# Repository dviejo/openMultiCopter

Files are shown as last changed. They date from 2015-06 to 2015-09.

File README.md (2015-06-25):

### Multi Copter Project ###

* Created by Diego Viejo

* Date of creation: 09/May/2015

* Distributed under Apache License V2.0

## Description ##

This project is for developing a working multi copter drone chassis. It is fully designed using [OpenScad](http://www.openscad.org "OpenScad"). The project arises after the great quadcopter design of Daniel Norée that you can find [here](http://www.thingiverse.com/thing:793425 "here"). This is robust and aesthetically perfect quad. But it don't fit different electronics nor copter's gears. As Daniel has its design frozen, I decided to make my own and take his as an inspiration. 

I'm trying to keep copter arms fully compatible with those from Daniel's design. So it will be possible to use his arms in my copter body and vice-versa.

My idea is to make this project fully parameterizable: the number of arms, size for the body, battery compartment and so on. 

For some parts of this project I'm using the nice writing routines from Harlan Martin. The complete package can be downloaded from [his repository on github](https://github.com/rohieb/Write.scad "writescad").

## Current Status: Design and Test

* Copter arm is finished. (Already printed and tested)
* Quadcopter body is finished (Already printed and tested)
* Quadcopter body cover is finished (Already printed and tested)
* Quadcopter battery compartment is finished (Already printed and tested)

** First Flight Performed!!!! ** 

[https://youtu.be/LpXG32mkR34](https://youtu.be/LpXG32mkR34)
[https://youtu.be/p5fSE5LHzbQ](https://youtu.be/p5fSE5LHzbQ)
[https://youtu.be/718BIuiu2yI](https://youtu.be/718BIuiu2yI)
[https://youtu.be/-O9PJhnjDc4](https://youtu.be/-O9PJhnjDc4)

## Pictures

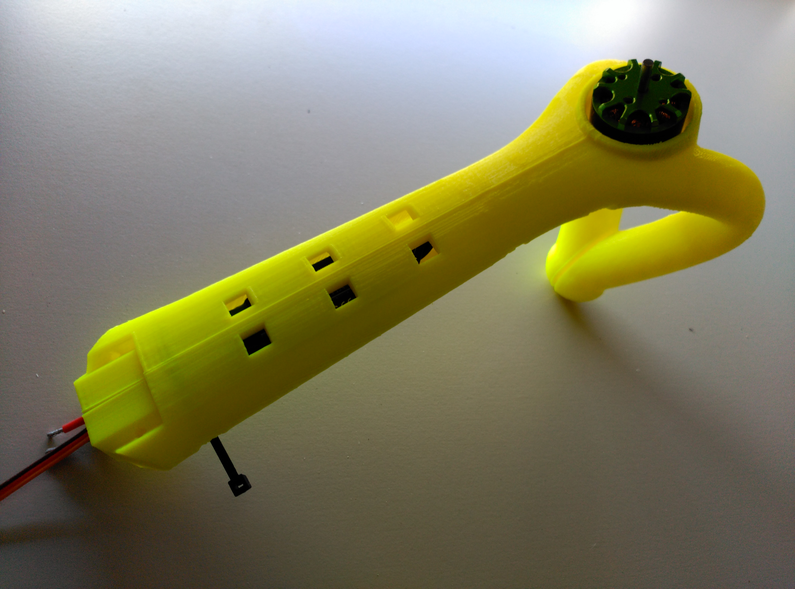
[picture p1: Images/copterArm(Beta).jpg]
copter arm mounted copter arm


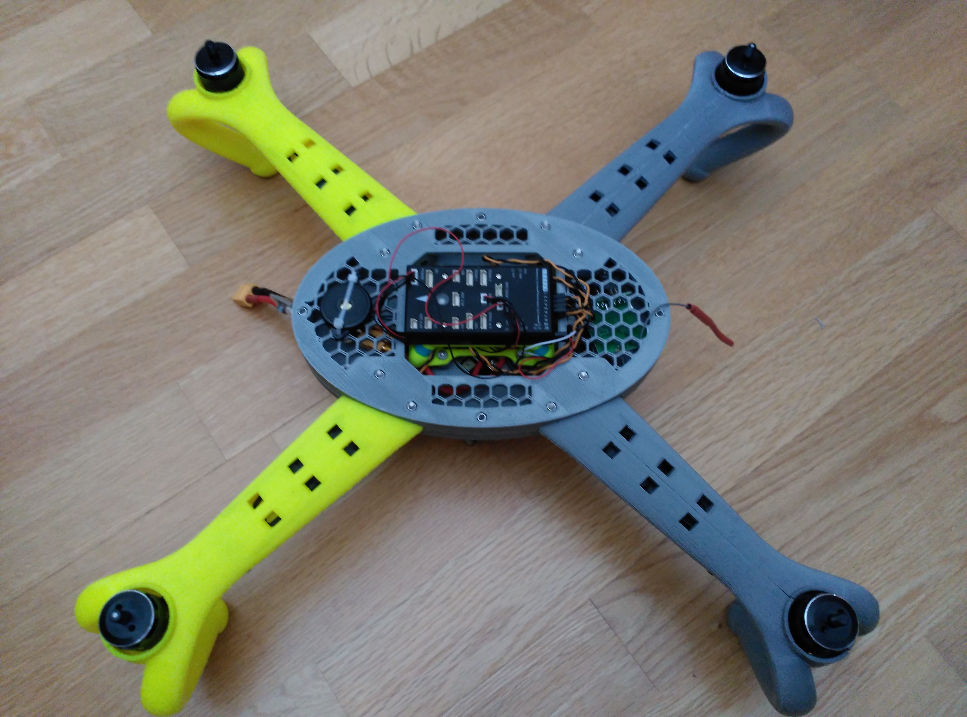
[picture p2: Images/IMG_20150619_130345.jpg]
main frame mounted main frame and arms


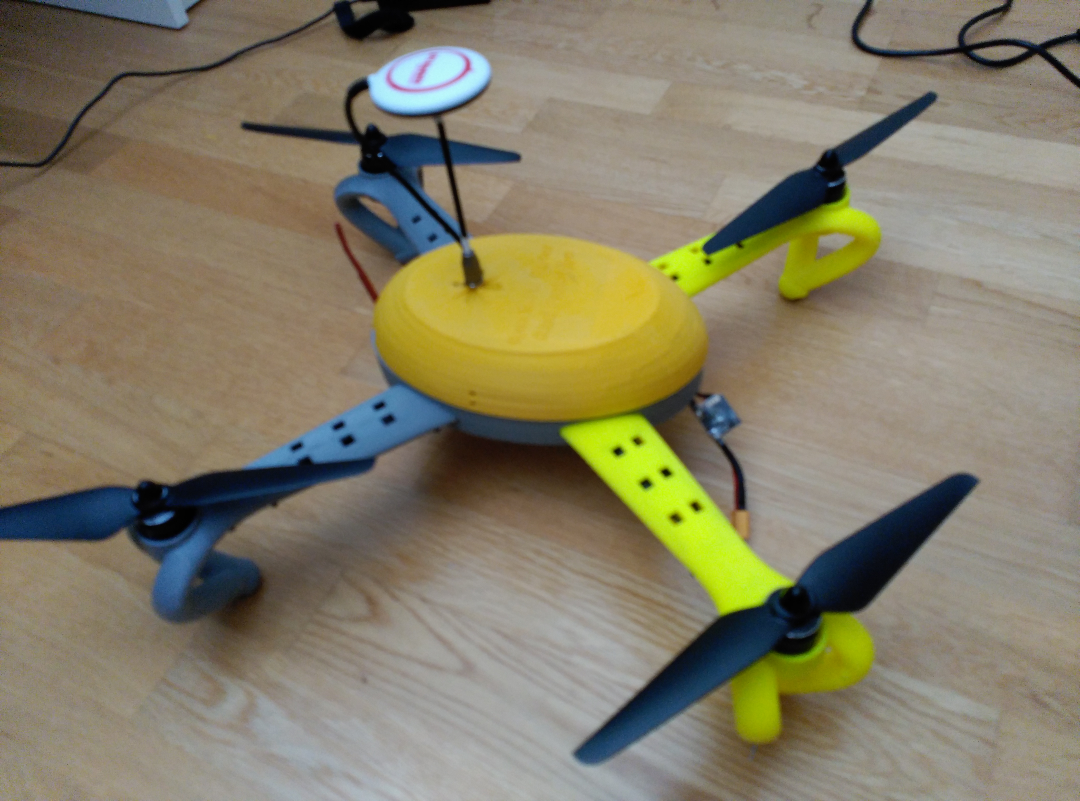
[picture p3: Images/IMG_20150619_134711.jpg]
complete copter V1 main frame and arms


More pictures can be found at [github repository](https://github.com/dviejo/openMultiCopter/tree/master/Images "github repository")

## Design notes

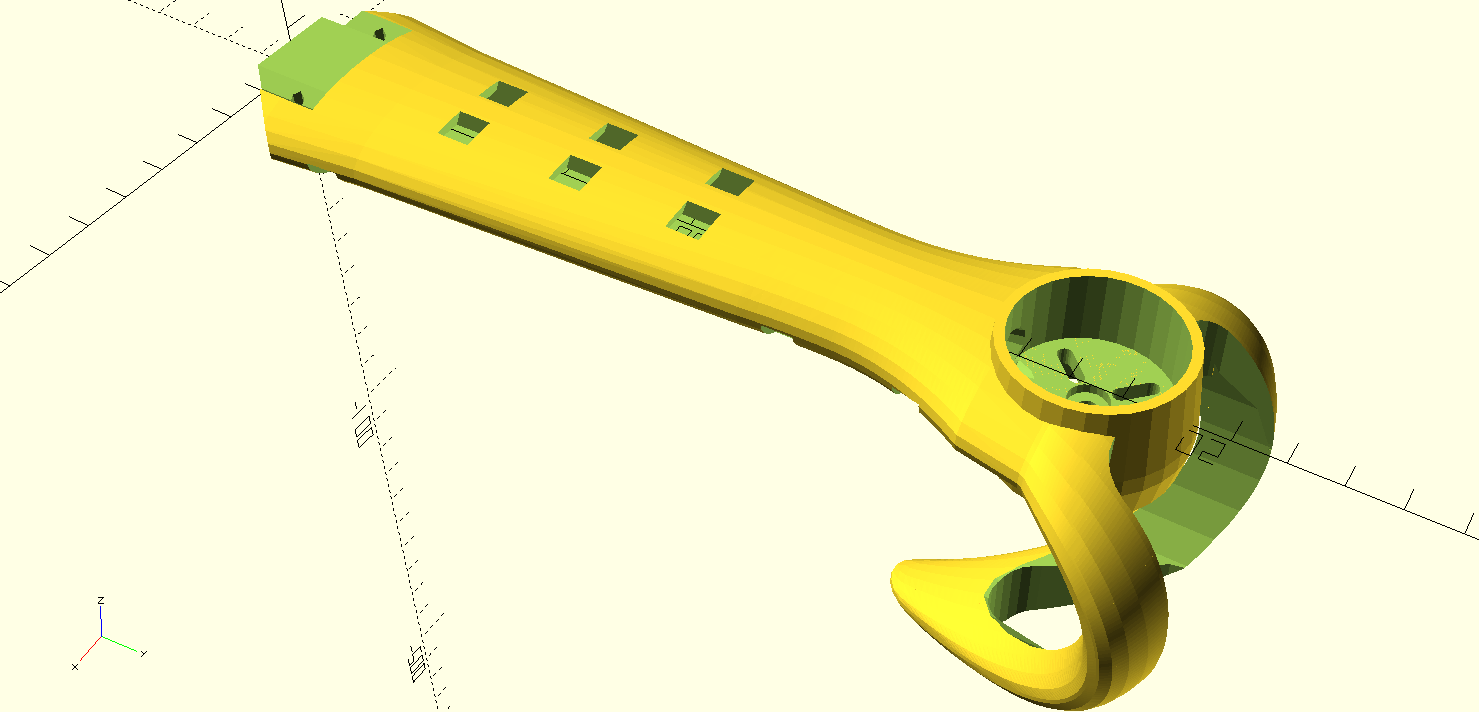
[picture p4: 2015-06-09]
Images/CopterArmComplete.png

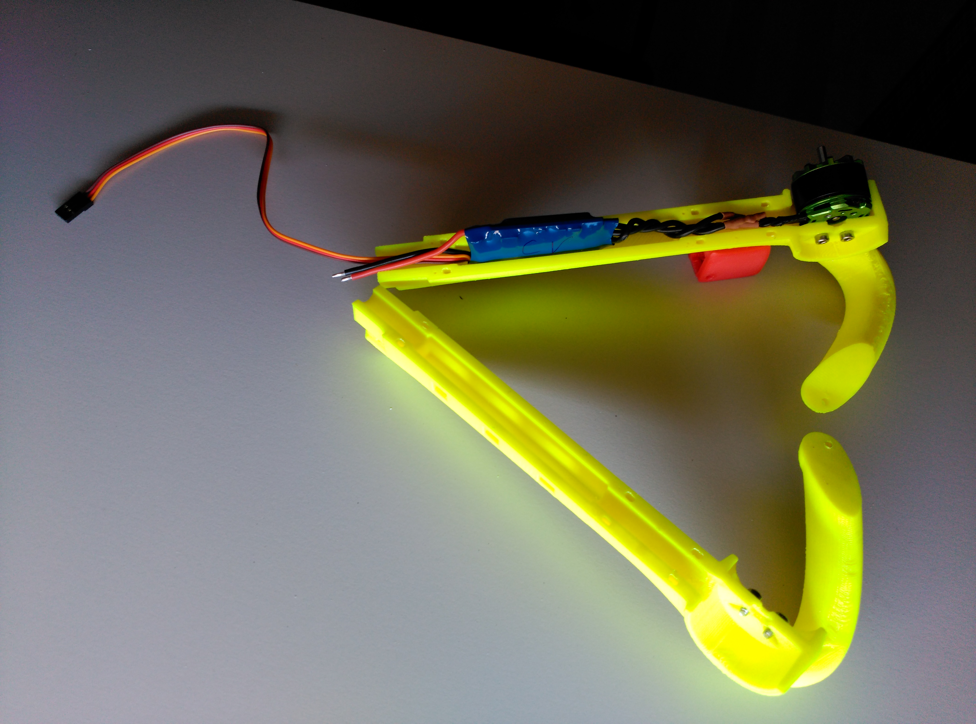
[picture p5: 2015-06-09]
Images/copterArm2(Beta).jpg

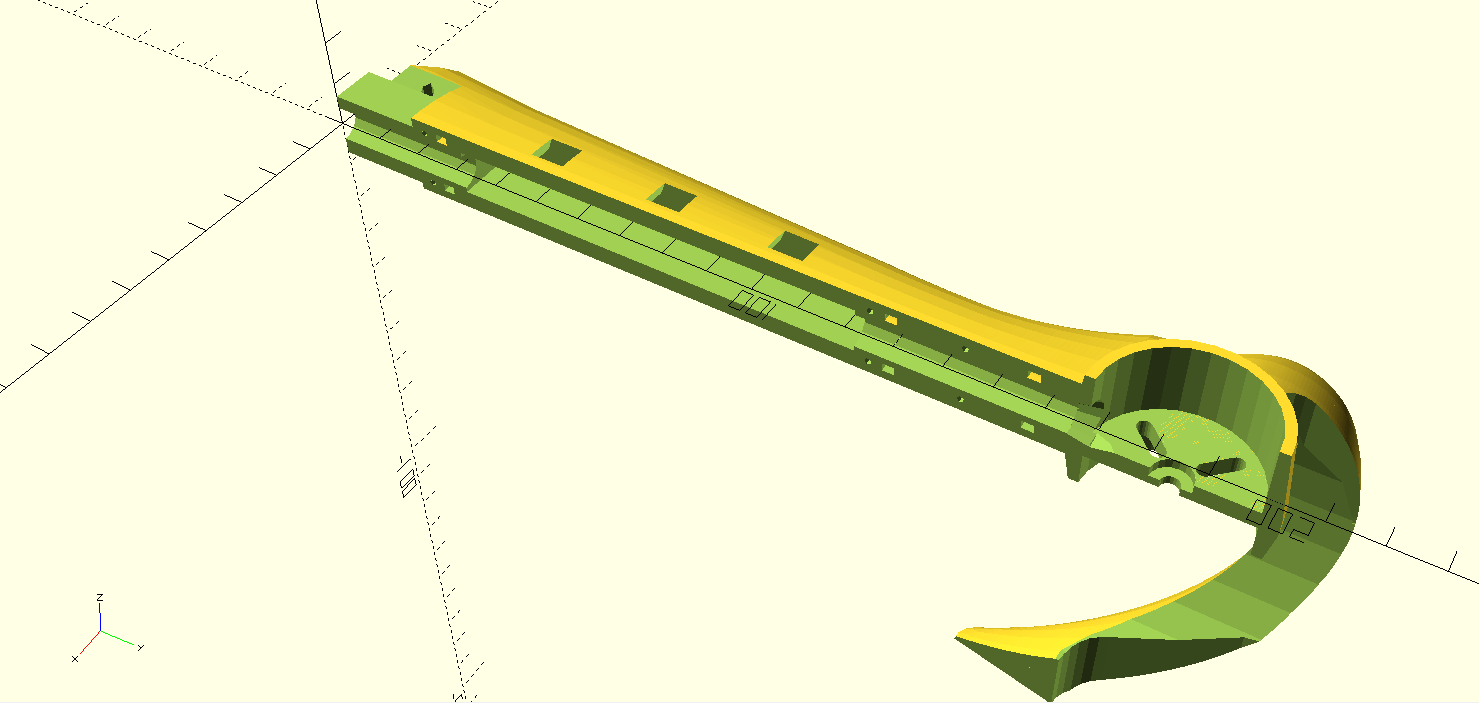
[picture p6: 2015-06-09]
Images/CopterArmPart1.png

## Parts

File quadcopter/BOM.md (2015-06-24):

# Open Multi Copter - Quad BoM #

## Bill Of Materials ##

> All the components that I used for building up this quad copter has been purchased from [RC-Innovations](rci-innovations.com "RC-Innovations") or [Hobbyking](http://www.hobbyking.com "Hobbyking"). Nevertheless, as this project is parametrizable, you can use any component you want and adapt the copter chassis to it.

1. Motors and propellers

 - [T-Motor AIR GEAR 350 Set](https://rc-innovations.es/Motores-multirrotores-aeromodelismo-brushless/TMotor-motores-para-multicopteros-drones-RC-Innovations-distribuidor-oficial/T-motor-pack-mot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 "T-Motor AIR GEAR 350 Set") 120€. This set includes 4 920kv motors, 4 20A ESCs and 4 (2CW + 2CCW) propellers
 
 - Alternatively, you can purchase [Multistar 350QX Blade Motor set](http://www.hobbyking.com/hobbyking/store/__54277__Multistar_350QX_Blade_Motor_set_4pcs_Box_2209_1200KV.html "Multistar 350QX Blade Motor set") (~59€) or [Multistar Elite - 2216-920 Box set](http://www.hobbyking.com/hobbyking/store/uh_viewItem.asp?idProduct=74770 "Multistar Elite - 2216-920 Box set") (~80€) and matched propellers. In these cases you will need also to purchase 4 ESCs like [HobbyKing 20A BlueSeries Brushless Speed Controller](https://www.hobbyking.com/hobbyking/store/uh_viewItem.asp?idProduct=39253 "HobbyKing 20A BlueSeries Brushless Speed Controller") (~10€ each)
 
2. Battery

 - Any LiPo 3S >2200 mAh will be ok. I have been using those: [Turnigy 2200mAh 3S 25C Lipo](https://www.hobbyking.com/hobbyking/store/__35819__Turnigy_2200mAh_3S_25C_Lipo_Pack_EU_Warehouse_.html "Turnigy 2200mAh 3S 25C Lipo") (~13€) and [Desire power V8 Series 3s 6000mAh 30C](https://rc-innovations.es/Baterias-para-drones-aviones-multicopteros-RC/Baterias-LiPo-multicopteros-aeromodelismo/Baterias-lipo-3s-calidad/desire-power-3s-6000-30c "Desire power V8 Series 3s 6000mAh 30C") (~60€).
 
3. [Power distribution](https://rc-innovations.es/Accesorios-aeromodelismo/Conectores-cables/Placa-de-potencia-soldaduras-multicoptero-negra "Power distribution") 4.25€

4. Electronics

 - [Pixhawk](https://rc-innovations.es/Multicopteros-drones-multirrotores-RPAs/multicopteros-Pixhawk/controladora-autopiloto-Pixhawk-avion-multicoptero-uav-RPAs-GPS-osd-telemetri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 "Pixhawk")
 
5. Radio transmitter. All you need is a (at least) 6 channel radio.

 - [FlySky FS-TH9X 8ch 2.4Ghz](https://rc-innovations.es/rc-transmiters/FlySky-rc-2.4Ghz/flysky-2.4g-9ch-radio-model-transmitterreceiver-fs-th9x-flysky "FlySky FS-TH9X 8ch 2.4Ghz") (~100€)
 
 - [Turnigy 9X 9Ch Transmitter](https://www.hobbyking.com/hobbyking/store/__8992__Turnigy_9X_9Ch_Transmitter_w_Module_8ch_Receiver_Mode_2_v2_Firmware_.html "Turnigy 9X 9Ch Transmitter") (~66€)
 
6. Anti Vibration Mount

 - You can print it out from [Thingiverse](http://www.thingiverse.com/thing:160655 "Thingiverse") and just buy [silicone dampers](https://rc-innovations.es/silicone-dampers.-4-units-siliconeballblue-rci-innovations-en "Silicone dampers").
 
7. Nuts and bolts

 - 18 M3 nuts. Nylon lock if possible.
 - 12 M3x20 bolts

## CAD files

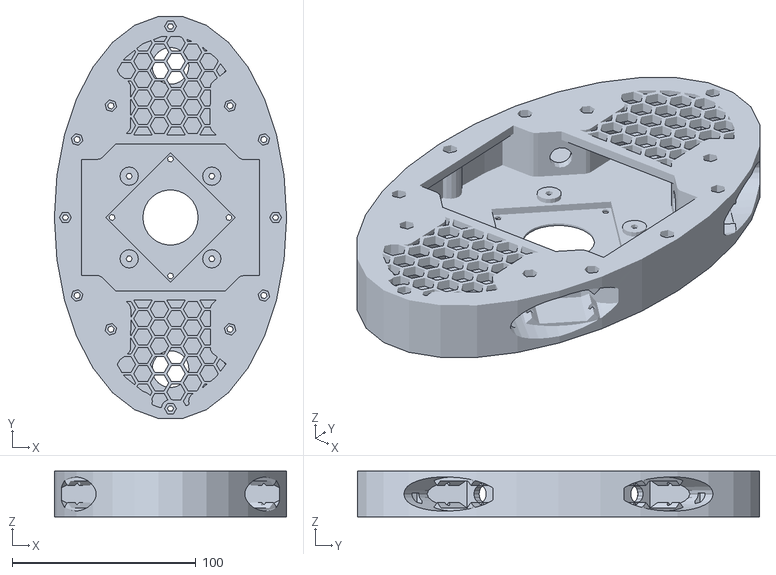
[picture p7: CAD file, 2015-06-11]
stl/mainPlatform.stl
126.4 x 218.8 x 25.0

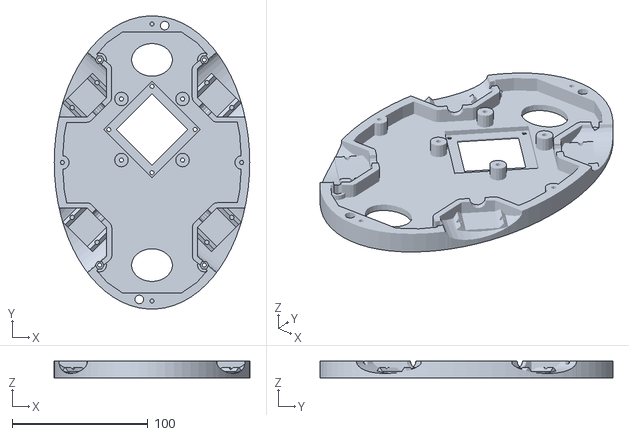
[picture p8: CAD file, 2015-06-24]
quadcopter/output/mainPlatformPart1.stl
144.0 x 215.8 x 12.5

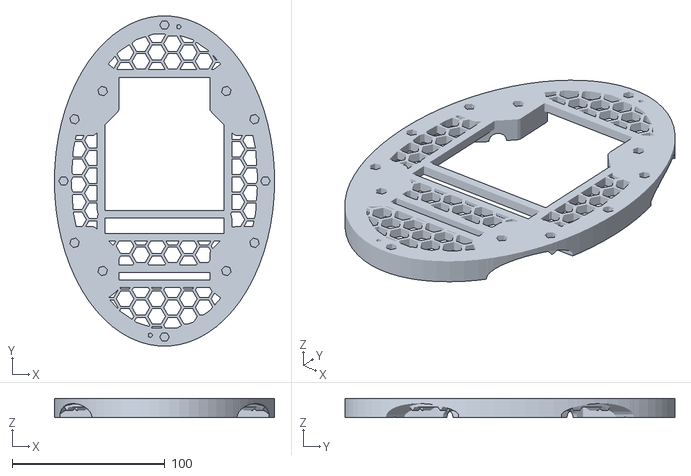
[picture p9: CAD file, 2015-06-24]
quadcopter/output/mainPlatformPart2.stl
144.0 x 215.8 x 12.5

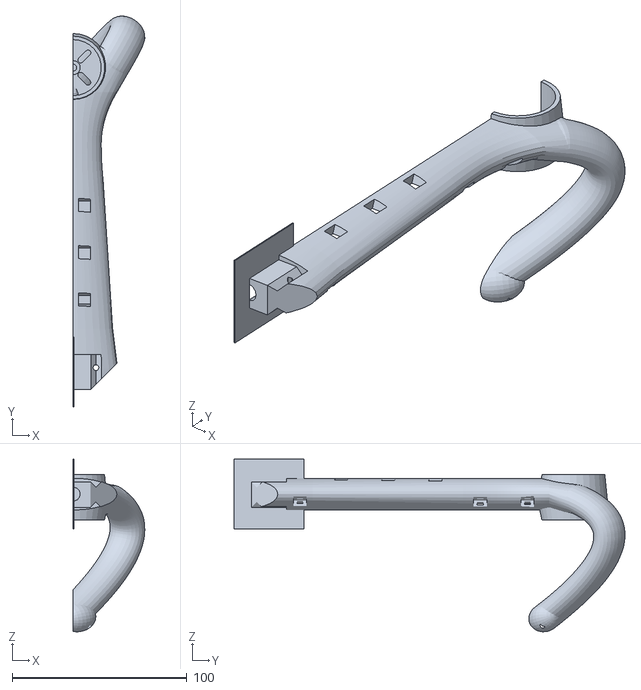
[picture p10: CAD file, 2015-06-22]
commons/output/copterArmCCWPart1.stl
40.9 x 223.5 x 98.8

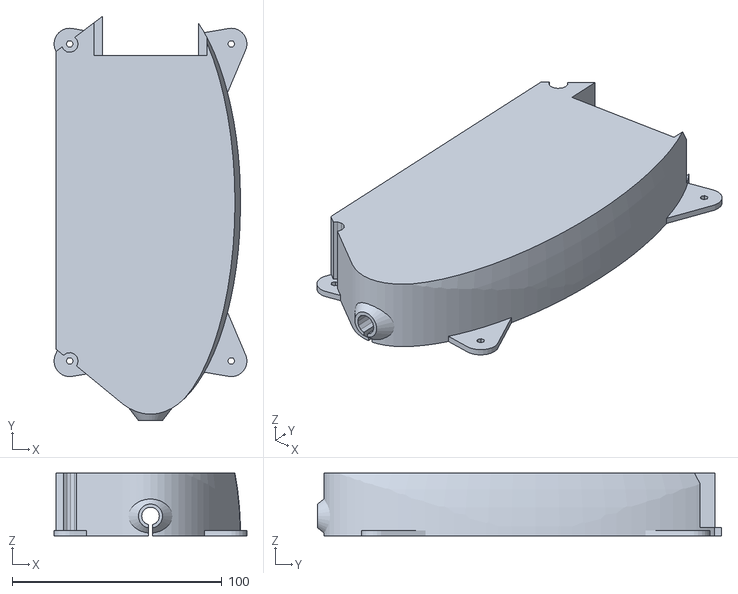
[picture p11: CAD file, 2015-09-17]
quadcopter/output/batteryCompartment_Turnigy5Ah3S.stl
92.0 x 192.7 x 30.0

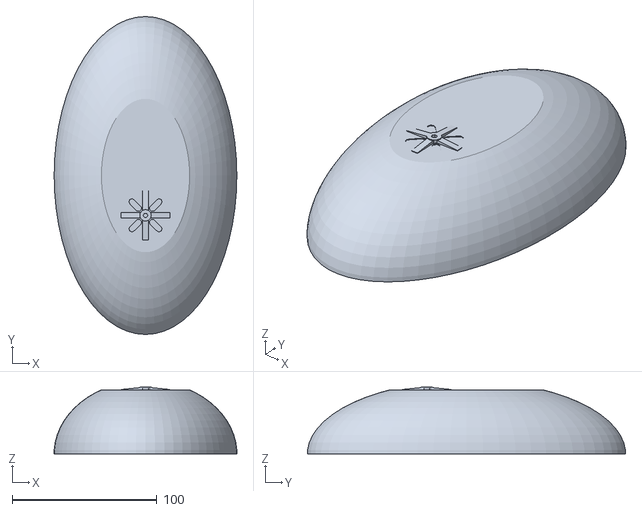
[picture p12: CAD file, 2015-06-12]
stl/cover.stl
126.2 x 219.7 x 46.2

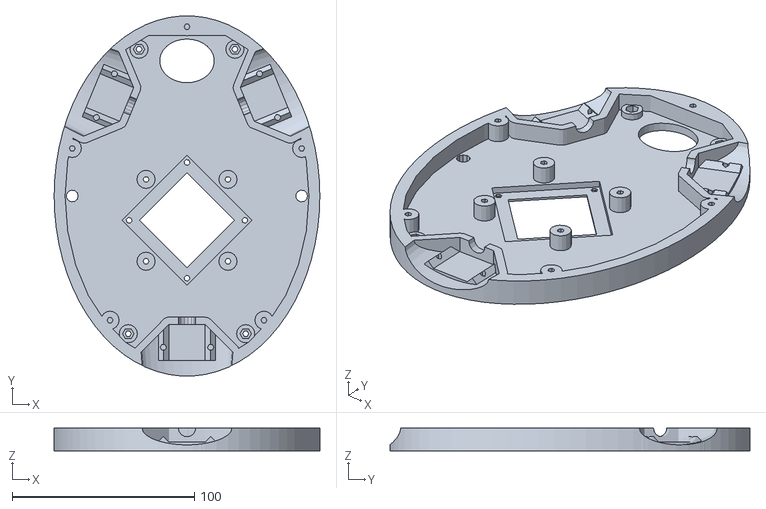
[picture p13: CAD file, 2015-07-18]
tricopter/output/base1.stl
146.0 x 197.8 x 12.5

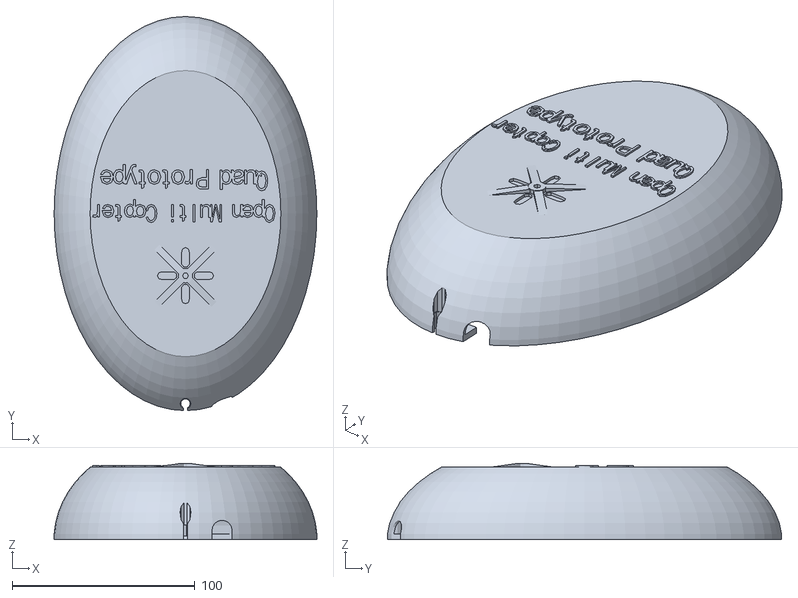
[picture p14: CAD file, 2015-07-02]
quadcopter/output/copterCover.stl
143.8 x 215.6 x 41.6

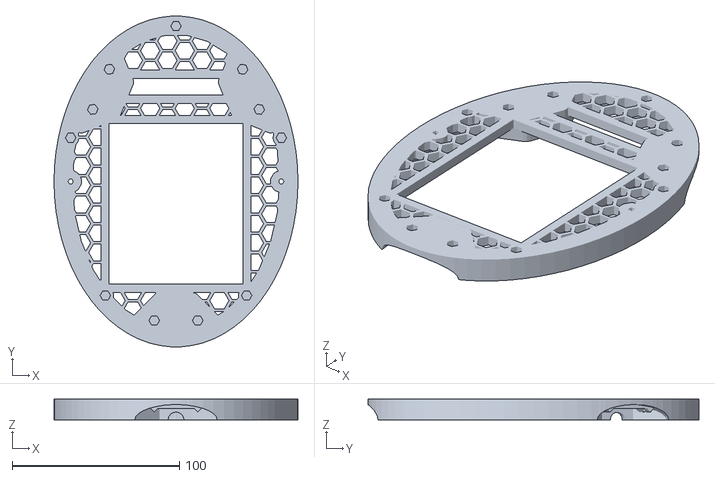
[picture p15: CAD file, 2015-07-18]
tricopter/output/base2.stl
146.0 x 197.8 x 12.5

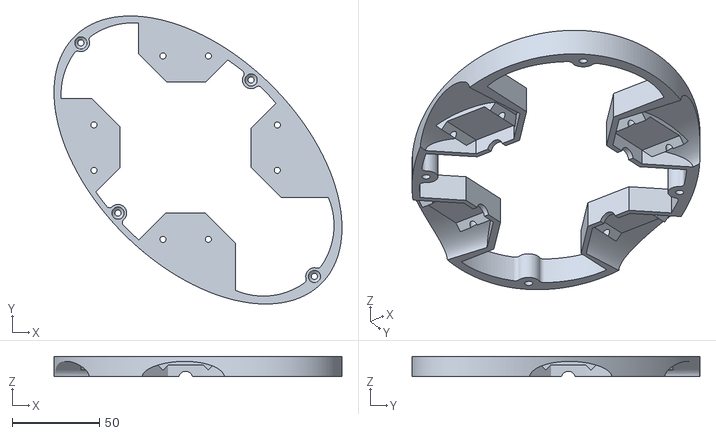
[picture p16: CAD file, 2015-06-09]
stl/OpenRC_Quad_Alpha_Body_Upper.stl
164.9 x 164.9 x 11.5

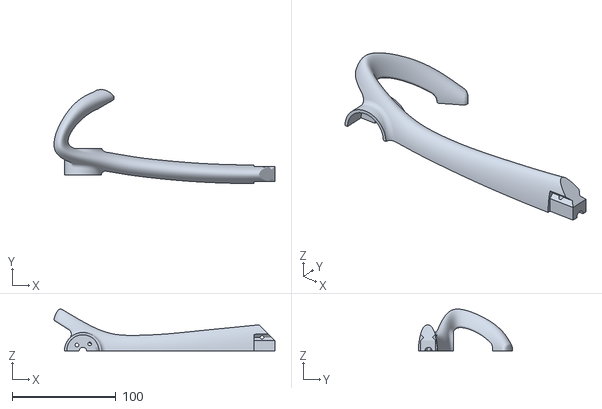
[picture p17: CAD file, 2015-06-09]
stl/OpenRC_Quad_Alpha_Arm_Part_1.stl
212.8 x 90.6 x 40.3

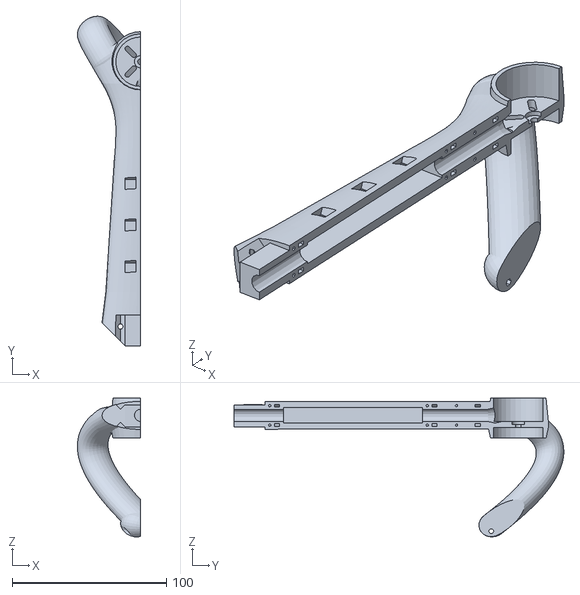
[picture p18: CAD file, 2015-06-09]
commons/output/copterArmPart1.stl
40.9 x 213.5 x 90.0

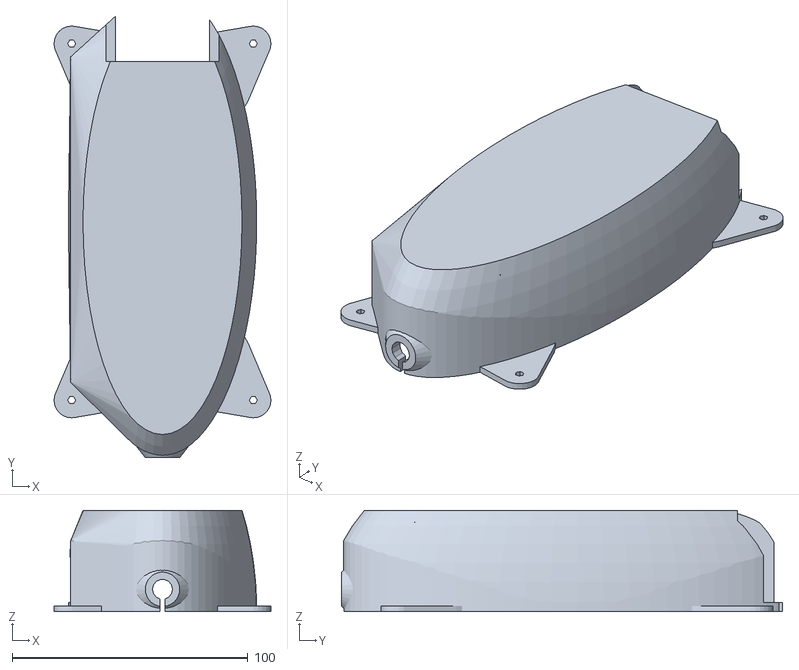
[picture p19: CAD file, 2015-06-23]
quadcopter/output/batteryCompartment.stl
92.0 x 187.2 x 43.0

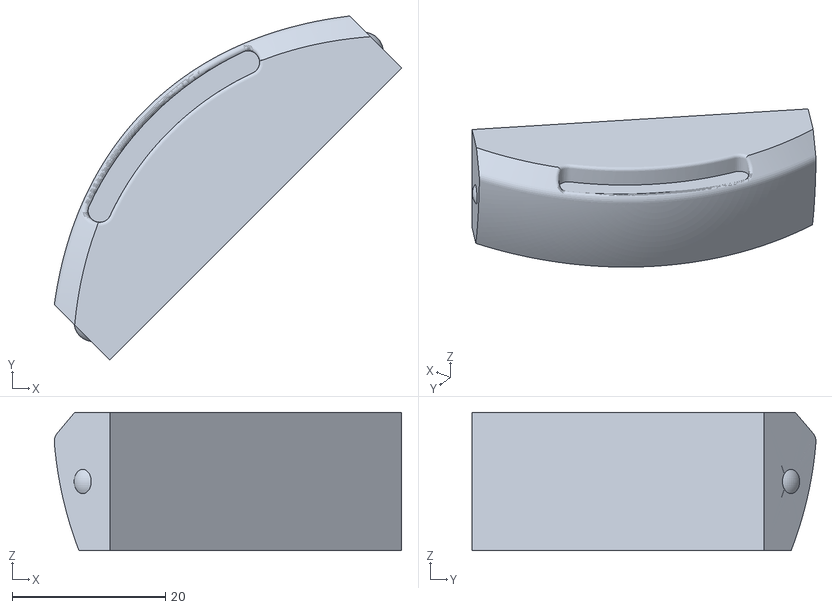
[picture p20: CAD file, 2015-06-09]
stl/OpenRC_Quad_Alpha_Battery_Compartment_Door.stl
45.3 x 44.8 x 18.0

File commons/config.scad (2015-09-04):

/**
 * config.scad
 * 
 * Constants and common methods used for the multi-copter
 * 
 */

//wire openning
wireDiameter = 8;


// suavizar las superficies curvas
//$fs= 1 ; 
//$fa= 1 ; 


////////motorMount
motorOuterDiam = 37;
motorInnerDiam = 32;

motorHeight = 26;

motorPlatformHeight = 7;
motorPlatformWidth = 3.75;

motorAxleDiam = 4;
bottomClearanceDiam = 8;
bottomClearanceHeight = 2.5;


///////////// armMount
entryWidth = 50.75/2;
entryHeight = 18.25/2;
entryDepth = 12;

outputWidth = 45/2; //49/2;
outputHeight = 18/2;
outputDepth = 8 +15; //For modelling, this is the position of the further ellipse


armLength = 184; //from the beginning of armMount/malePart to the center of motorMount

//auxiliary method
module oval(w,h, height, center = false) {
 scale([1, h/w, 1]) cylinder(h=height, r=w, center=center);
}

//auxiliary method
module ellipsoid(w,h, center = false) {
 scale([1, h/w, 0.8]) sphere(r=w, $fn=60);
}


//auxiliary method
module nestedHull()
{
  for(i=[0:$children-2])
    hull()
    {
      children(i);
      children(i+1);
    }
}

//hexer module
scale = 1.15;
hexagon_d = 10*scale;
hexagon_x = 9*scale;
hexagon_y = 5*scale;
hexagon_h = 50; // centered

min_x = - 150;
max_x = 150;
min_y = -100;
max_y = 100;

wall_t = 5;
module hollowify()
difference(convexity=10){
    children(0); 
    linear_extrude(center=true,convexity=10){
        difference(){
            // hexagon array
            for(
                x=[min_x:hexagon_x*2:max_x], 
                y=[min_y:hexagon_y*2:max_y]
            ) translate([x, y, 0]) {
                circle(d=hexagon_d,  center=true, $fn=6);
                translate([hexagon_x, hexagon_y, 0]) circle(d=hexagon_d, center=true, $fn=6);
            }

            minkowski(){
                difference(){
                    translate([min_x, min_y, 0])
                        square([hexagon_x + max_x-min_x, hexagon_y + max_y-min_y]);
                    projection() children(0); 
                }
                circle(r=wall_t);
            }
        }
    }
}

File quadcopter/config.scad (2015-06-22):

/**
 * Quad Copter configuration file
 *
 */

//Main electronics dimensions

//ardupilot
elecWidth = 40.64;
elecLength = 66.42;
elecHolesWidth = 35.31;
elecHolesHeight = 61.09;

// Omnimac 3DR APM Anti Vibration Mount
monimacWidth = 58;
monimacLength = 97;
monimacHolesWidth = 45;
monimacHolesHeight = 45;

wallThick = 6;

baseLength = 108;

baseWidth = 72;

baseHeight = 25;

//electronic's openning. Shared by mainPlatform and cover
openningLength = 78;
openningWidth = 87;

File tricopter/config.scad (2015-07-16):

/**
 * Tricopter config file
 * 
 * Created by Diego Viejo
 */

// Omnimac 3DR APM Anti Vibration Mount
monimacWidth = 58;
monimacLength = 97;
monimacHolesWidth = 45;
monimacHolesHeight = 45;


//front arms angle in the range [45:90]
frontAngle = 45 + 45/2;

wallThick = 6;

baseLength = 99;

baseWidth = 73;

baseHeight = 25;

//electronic's openning. Shared by mainPlatform and cover
openningLength = 80;
openningWidth = 96;

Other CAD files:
quadcopter/Letters.dxf
commons/output/copterArmCWPart1.stl
commons/output/copterArmCCWPart2.stl
commons/output/copterArmCWPart2.stl
commons/armMount.scad
Electronics/pixhawk.scad
commons/copterArm.scad
commons/motorMount.scad
commons/output/armMountTest.stl
commons/output/copterArmPart2.stl
quadcopter/batteryCompartment.scad
quadcopter/cover.scad
quadcopter/mainPlatform.scad
stl/OpenRC_Quad_Alpha_Arm_Part_2.stl
stl/OpenRC_Quad_Alpha_Battery_Compartment.stl
stl/OpenRC_Quad_Alpha_Body_Lower.stl
stl/OpenRC_Quad_Alpha_Top_Cover.stl
stl/copterArm.stl
test.scad
tricopter/mainPlatform.scad
tricopter/tail.scad
writescad/Write.scad

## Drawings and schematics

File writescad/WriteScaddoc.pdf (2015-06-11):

p1

## WriteScad

By Harlan Martin
harlan@sutlog.com
January 2012

Version 2
Added support for future font selection (default is Letters.dxf) Added WriteCube module
Added Rotate for text (rotates on the plane of the text)
Added writesphere module

NOTE: These routines require openscad version 2011.12 or later

http://www.openscad.org/

-o-

## write()

Note about strings:
1... | The quote " symbol cannot be inserted into a string alone Either use \" or just the single quote' will show as "
2... | The \ is used for special text characters, so use the bar | to show the back slash \

Usage

Put the files (write.scad) and (letters.dfx) in the
| same directory as your project.

write("Hello World!",t=3,h=5,center=true);

(t=mm) (optional) The thickness of the letters in mm.
| The default is 1mm if not specified

(h=mm)(optional) The height of the letters in mm.
| The default is 4mm if not specified

(rotate=degrees) Rotates the text along the plane it is written on.

(center=boolean) (optional) Centers the text at default coordinates. Examples:

use <write.scad> // Dont forget to include this line

//example1: Uses all declarations..
| translate([20,15,0]) write("Example 1",t=4,h=5.75,center=true);

//example2: Quick and easy
| write("That was easy!",h=12);

//example3: move and rotate(front) (remember to translate..then rotate)
| translate([0,0,10]) rotate(90,[1,0,0]) // rotate around the x axis write("Rotate +X 90 (front)",t=2);

//example4: move and rotate(left side)
| translate([0,0,20]) rotate(90,[1,0,0]) // rotate around the x axis rotate(90,[0,-1,0]) // rotate around the y axis write("Rotate +X 90 and -Y 90 (left side)");

//example5: move and rotate(right side)
| translate([0,0,30]) rotate(90,[1,0,0]) // rotate around the x axis rotate(90,[0,1,0]) // rotate around the y axis write("Rotate +X 90 and +Y 90 (right side)");

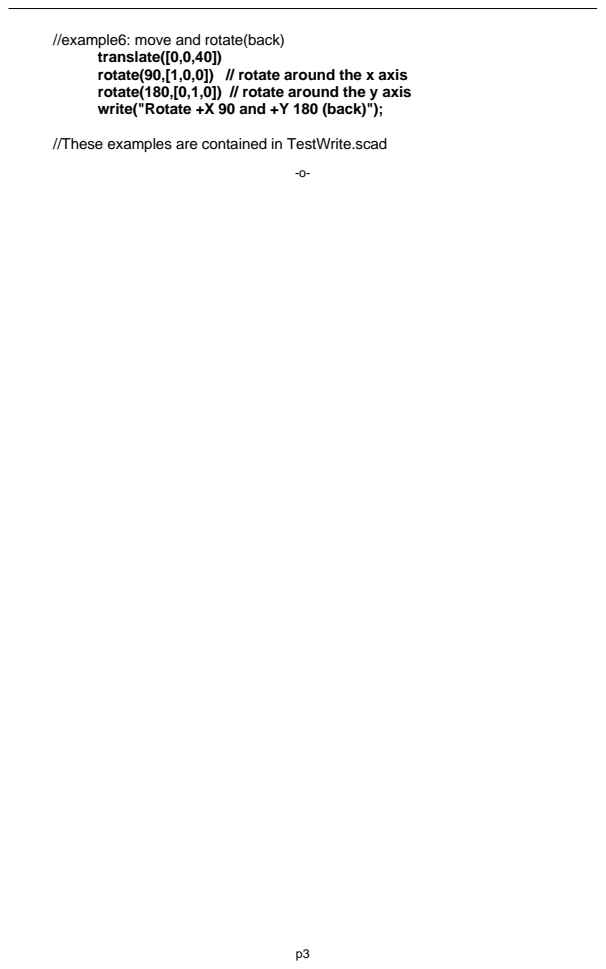
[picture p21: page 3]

//example6: move and rotate(back)

translate([0,0,40])
rotate(90,[1,0,0]) // rotate around the x axis
rotate(180,[0,1,0]) // rotate around the y axis
write("Rotate +X 90 and +Y 180 (back)");

//These examples are contained in TestWrite.scad

## writecube()

For these examples, assume we have the cube: use <write.scad>
translate([10,20,30])
cube(30,center=true);
text where and size
The values for text=, where= and size= are required, but if the values are entered in this order, then the commands are not required. These three examples produce the same results.

writecube(text="text", where=[10,20,30], size=[30,30,30]); or
writecube("text",[10,20,30], [30,30,30]);
or
writecube("text",[10,20,30],30);

text is written on the center front of a cube that is 30mm on all sides, and is centered at [10,20,30]

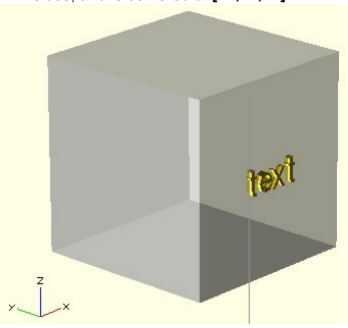
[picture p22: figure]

text="whatever text you want to write"
where= the center coordinates of the box
size = size of cube. If the cube is not square, use the format [xsize,ysize,zsize] If it is the same on all sides, just give the size ie. 30
face=
By default, writecube() will write on the front face of the box.
This assumes that x=left to right, y=front to back, z=bottom to top. To write on the other sides, use: face="top",face="bottom",face="back",face="front", face="left" or face="right"

writecube("Howdy!!",[10,20,30],30,face="left");

will print Howdy!! on the center left of the box.

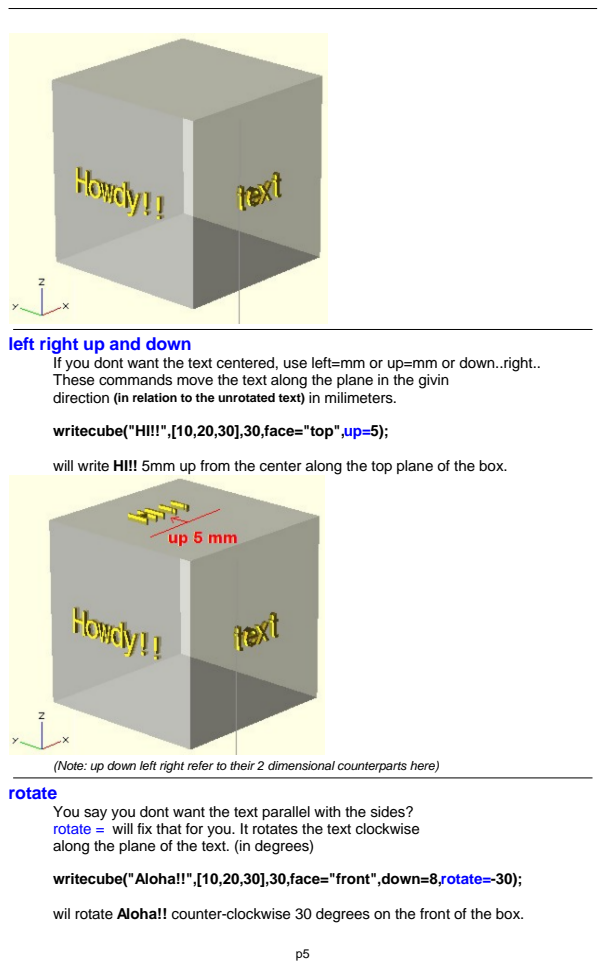
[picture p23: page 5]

left right up and down

If you dont want the text centered, use left=mm or up=mm or down..right..
These commands move the text along the plane in the givin
direction (in relation to the unrotated text) in milimeters.

writecube("HI!!",[10,20,30],30,face="top",up=5);

will write HI!! 5mm up from the center along the top plane of the box.

(Note: up down left right refer to their 2 dimensional counterparts here)
rotate

You say you dont want the text parallel with the sides?
rotate = will fix that for you. It rotates the text clockwise
along the plane of the text. (in degrees)

writecube("Aloha!!",[10,20,30],30,face="front",down=8,rotate=-30);

wil rotate Aloha!! counter-clockwise 30 degrees on the front of the box.

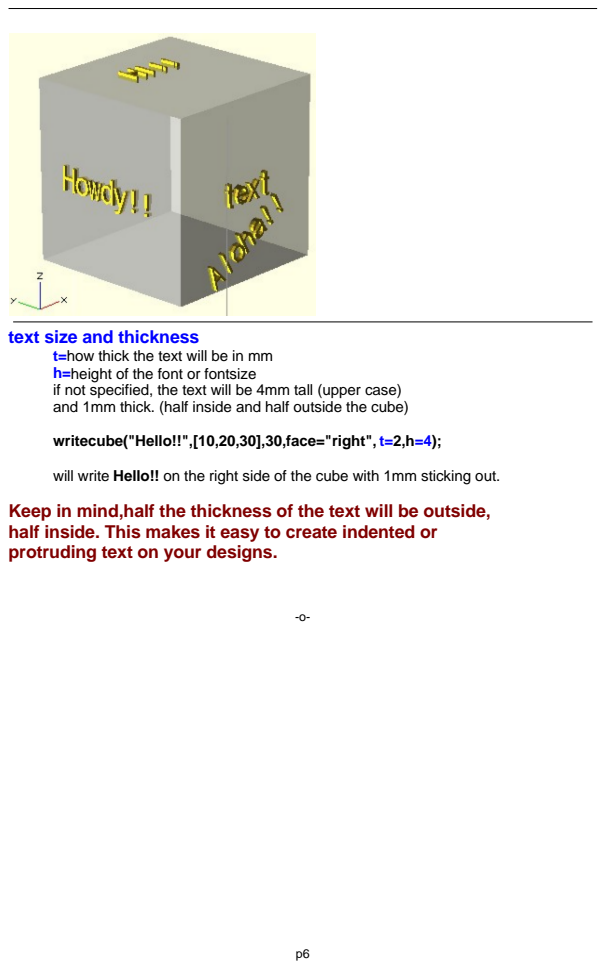
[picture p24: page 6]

text size and thickness

t=how thick the text will be in mm
h=height of the font or fontsize
if not specified, the text will be 4mm tall (upper case)
and 1mm thick. (half inside and half outside the cube)

writecube("Hello!!",[10,20,30],30,face="right", t=2,h=4);

will write Hello!! on the right side of the cube with 1mm sticking out.
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

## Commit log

2015-06-09 copter project moved from 3d-Models repository
    [OpenRC_Quad_Alpha_Arm_Part_1.stl, OpenRC_Quad_Alpha_Arm_Part_2.stl, OpenRC_Quad_Alpha_Battery_Compartment.stl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]
2015-06-10 armMount female shrinked
    [armMount.scad]
2015-06-10 tunning up armMount female part
    [armMount.scad]
2015-06-10 holder for connections board
    [mainPlatform.scad]
2015-06-10 armMount nut and head holes added to female part
    [armMount.scad]
2015-06-10 mainPlatform resized
    [config.scad, mainPlatform.scad]
2015-06-10 main Platform parts 1 & 2 generated
    [mainPlatformPart1.stl, mainPlatformPart2.stl]
2015-06-11 mainPlatform stl generated for the development of next parts
    [mainPlatform.stl]
2015-06-11 quad cover holder for GPS added
    [cover.scad]
2015-06-11 writescad folder added
    [Letters.dxf, Write.scad]
2015-06-11 quad cover holder for GPS modified
    [cover.scad]
2015-06-11 armMount female part updated
    [armMount.scad]
2015-06-11 motor mount minor changes
    [motorMount.scad]
2015-06-11 copter arm reworked to fit TMotor's ESC
    [copterArm.scad]
2015-06-11 copter arm stls generated
    [copterArm.scad, copterArmCCWPart1.stl, copterArmCCWPart2.stl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]
2015-06-11 mainPlatform tolerances updated
    [mainPlatform.scad]
2015-06-12 copterArm. TMotor ESC holder improved
    [copterArm.scad]
2015-06-12 copterArm stl generated
    [copterArmCCWPart1.stl, copterArmCCWPart2.stl, copterArmCWPart1.stl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]
2015-06-12 electronics oppening for quad now shared from config.scad
    [config.scad, cover.scad, mainPlatform.scad]
2015-06-12 Electronics modeling started
    [pixhawk.scad]
2015-06-12 mainPlatform electronics lifted up
    [mainPlatform.scad, pixhawk.scad]
2015-06-12 cover attaching gear moved
    [cover.scad, cover.stl]
2015-06-12 platform and cover adjustments
    [cover.scad, mainPlatform.scad]
2015-06-14 adapting mainPlatform
    [config.scad, mainPlatform.scad, mainPlatformPart1.stl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]
2015-06-15 platform hole for battery connection updated
    [mainPlatform.scad]
2015-06-15 main platform stl parts generated
    [mainPlatformPart1.stl, mainPlatformPart2.stl]
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2015-06-16 Quad cover ready to print
    [Letters.dxf, cover.scad]
2015-06-16 copterCover stl generate
    [copterCover.stl]
2015-06-16 cleaning up cover
    [cover.scad]
2015-06-16 cover printed, then modifications performed
    [cover.scad]
2015-06-16 quad cover stl generated
    [copterCover.stl]
2015-06-17 third revision of quad cover after printing
    [cover.scad]
2015-06-17 cover stl generated
    [copterCover.stl]
2015-06-17 ellipsoid module moved from copterCover to commons/config.scad
    [config.scad]
2015-06-17 quad cover minor changes. Further modifications needed
    [copterCover.stl, cover.scad]
2015-06-17 quad battery compartment created
    [batteryCompartment.scad]
2015-06-18 quad cover rework
    [cover.scad]
2015-06-19 new operative opennings for quad cover
    [cover.scad]
2015-06-19 copter cover stl generated
    [copterCover.stl]
2015-06-19 battery compartment ready to print
    [batteryCompartment.scad]
2015-06-19 battery compartment stl generated
    [batteryCompartment.stl]
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2015-06-19 quad battery compartment rework
    [batteryCompartment.scad]
2015-06-19 quad batteryCompartment stl generated
    [batteryCompartment.stl]
2015-06-20 start quad cover redesign
    [cover.scad, mainPlatform.scad]
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2015-06-22 quad's mainPlatform stl generated
    [mainPlatformPart1.stl, mainPlatformPart2.stl]
2015-06-22 support for copter arm printing added
    [copterArm.scad]
2015-06-23 quad cover main revision
    [cover.scad]
2015-06-23 quad copter cover stl generated
    [copterCover.stl]
2015-06-23 quad 6000mAh battery hoder adapted to the new dims
    [batteryCompartment.scad]
2015-06-23 re-structuring output. Moving files to commons/output
    [armMountTest.stl, copterArmCCWPart1.stl, copterArmCCWPart2.stl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]
2015-06-23 re-structuring output. Moving files to quadcopter/output. Older output folder has been deleted
    [batteryCompartment.stl, copterCover.stl, mainPlatformPart1.stl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]
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2015-06-24 quad main platform stl generated
    [mainPlatformPart1.stl, mainPlatformPart2.stl]
2015-06-24 adjusting quad cover to save arms mounting bolts
    [cover.scad]
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2015-07-01 change receiver antena holder
    [cover.scad]
2015-07-02 quad Cover. Support structure reinforced
    [cover.scad]
2015-07-02 quad cover receiver antenna holder rework
    [cover.scad]
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2015-07-03 joints relocated and electronic pods added
    [config.scad, mainPlatform.scad]
2015-07-16 tricopter main platform gets electronics openning
    [config.scad, mainPlatform.scad]
2015-07-16 tricopter main platform ready to be printed
    [config.scad, mainPlatform.scad]
2015-07-16 tricopter main platform stl generated
    [base1.stl, base2.stl]
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2015-07-18 tricopter mainplatform conection beams updated
    [mainPlatform.scad]
2015-07-18 tricopter mainPlatform stl generated. Ready to print
    [base1.stl, base2.stl]
2015-07-20 tricopter tail. Servo modeled
    [tail.scad]
2015-07-21 motor mount config parameters moved to commons/config.scad
    [config.scad, motorMount.scad]
2015-09-04 development of tricopter tail. Work in progress
    [config.scad, motorMount.scad, tail.scad]
2015-09-17 Turnigy 5Ah 3S 25C 142x50x20 added to battery descriptions for battery compartment
    [batteryCompartment.scad]
2015-09-17 battery compartment stl generated for Turnigy 5Ah
    [batteryCompartment_Turnigy5Ah3S.stl]
